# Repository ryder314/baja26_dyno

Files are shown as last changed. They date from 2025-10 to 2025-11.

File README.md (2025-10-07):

# baja26_dyno
All files related to the motor dyno built by/for Texas A&M's Baja SAE 2026

The motor dyno makes use of a mechanical hydraulic pump connected to the
engine, which pumps hydraulic fluid around a tank with a restrictor controlled
by a stepper motor.
The designed PCB makes use of an XFW-HX711 module to read a load cell, an A4988
stepper driver for controlling flow restriction, as well as up to two RPM sensors
for engine RPM and eventually for primary/secondary sheave RPM when testing with
the e-CVT.
The design uses a Luckfox Lyra as the devboard to process and store data. This
board runs Buildroot Linux and handles all reading of inputs, calculation of
outputs, and storage/display of results.

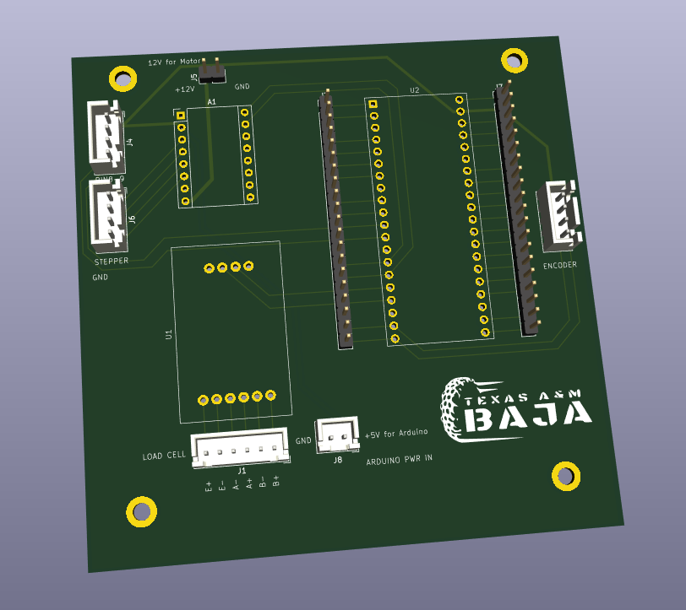
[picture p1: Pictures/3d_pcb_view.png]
3D View of the PCB for the Motor Dyno


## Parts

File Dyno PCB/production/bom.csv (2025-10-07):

Designator | Footprint | Quantity | Value | LCSC Part #
A1 | Pololu_Breakout-16_15.2x20.3mm | 1 | Pololu_Breakout_A4988
J1 | JST_XH_B6B-XH-A_1x06_P2.50mm_Vertical | 1 | Conn_01x06
J2, J4, J6 | JST_XH_B4B-XH-A_1x04_P2.50mm_Vertical | 3 | Conn_01x04
J3, J7 | PinHeader_1x20_P2.54mm_Vertical | 2 | Conn_01x20_Pin
J5 | PinHeader_1x02_P2.54mm_Vertical | 1 | Conn_01x02
J8 | JST_XH_B2B-XH-A_1x02_P2.50mm_Vertical | 1 | Conn_01x02_Socket
U1 | XFW_HX711 | 1 | ~
U2 | Untitled | 1 | ~

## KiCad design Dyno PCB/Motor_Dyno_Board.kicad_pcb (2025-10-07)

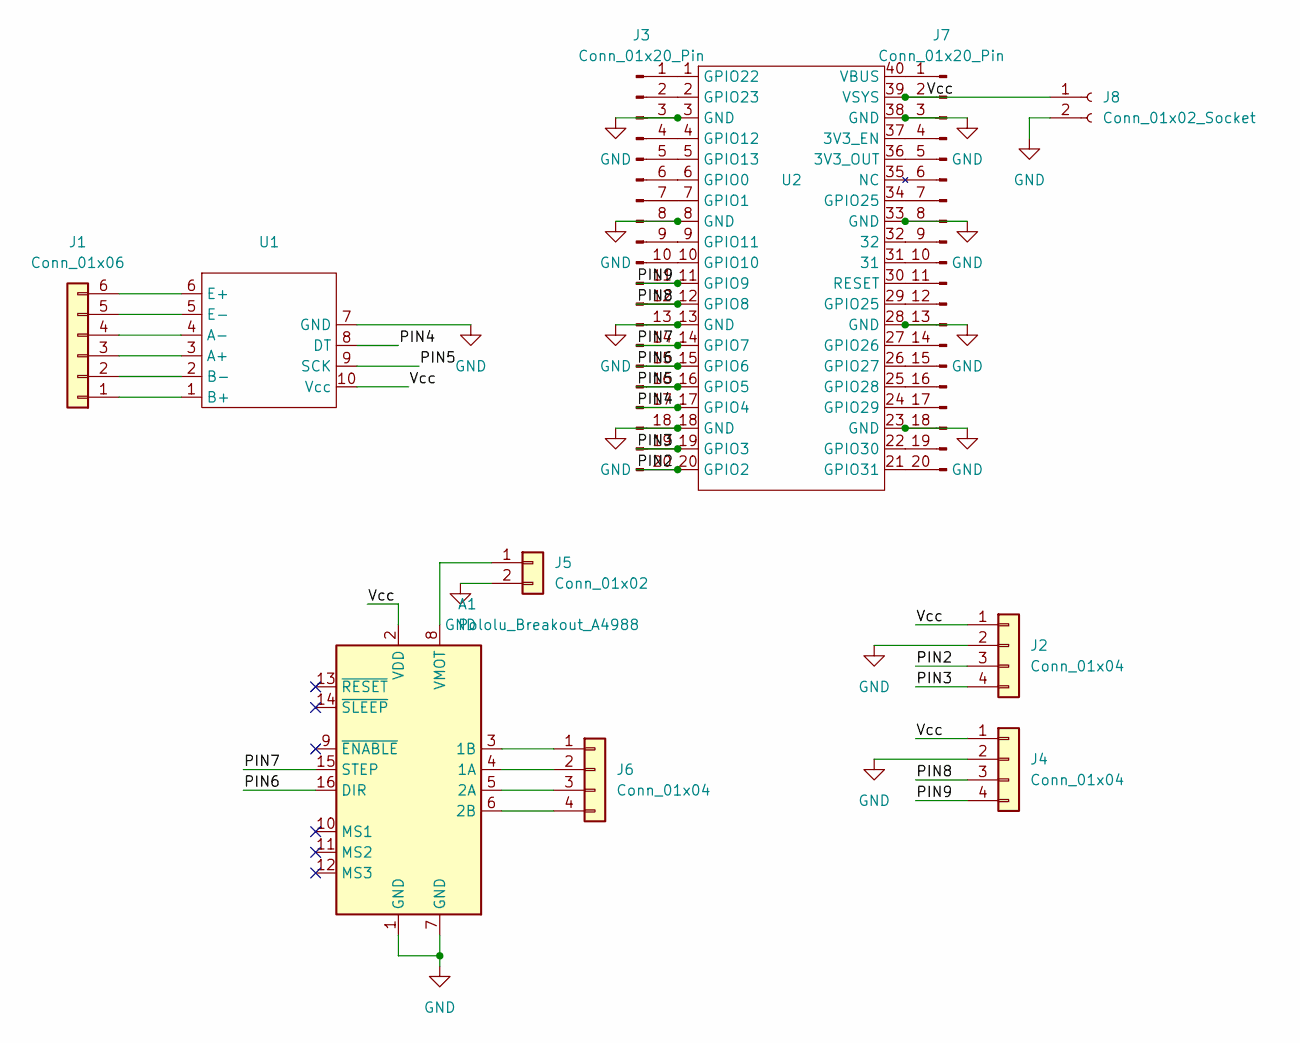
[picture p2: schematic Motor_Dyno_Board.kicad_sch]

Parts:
A1: Pololu_Breakout_A4988; Pololu_Breakout-16_15.2x20.3mm
J1: Conn_01x06; JST_XH_B6B-XH-A_1x06_P2.50mm_Vertical
J2, J4, J6: Conn_01x04; JST_XH_B4B-XH-A_1x04_P2.50mm_Vertical
J3, J7: Conn_01x20_Pin; PinHeader_1x20_P2.54mm_Vertical
J5: Conn_01x02; PinHeader_1x02_P2.54mm_Vertical
J8: Conn_01x02_Socket; JST_XH_B2B-XH-A_1x02_P2.50mm_Vertical
U1: XFW_HX711
U2: Untitled

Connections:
/PIN2: J2.3, J3.20, U2.20 (GPIO2)
/PIN3: J2.4, J3.19, U2.19 (GPIO3)
/PIN4: J3.17, U1.8 (DT), U2.17 (GPIO4)
/PIN5: J3.16, U1.9 (SCK), U2.16 (GPIO5)
/PIN6: A1.16 (DIR), J3.15, U2.15 (GPIO6)
/PIN7: A1.15 (STEP), J3.14, U2.14 (GPIO7)
/PIN8: J3.12, J4.3, U2.12 (GPIO8)
/PIN9: J3.11, J4.4, U2.11 (GPIO9)
/Vcc: A1.2 (VDD), J2.1, J4.1, J7.2, J8.1, U1.10 (Vcc), U2.39 (VSYS)
GND: A1.1 (GND), A1.7 (GND), J2.2, J3.3, J3.8, J3.13, J3.18, J4.2, J5.2, J7.3, J7.8, J7.13, J7.18, J8.2, U1.7 (GND), U2.3 (GND), U2.8 (GND), U2.13 (GND), U2.18 (GND), U2.23 (GND), U2.28 (GND), U2.33 (GND), U2.38 (GND)
unnamed: A1.4 (1A), J6.2
unnamed: A1.3 (1B), J6.1
unnamed: A1.5 (2A), J6.3
unnamed: A1.6 (2B), J6.4
unnamed: A1.8 (VMOT), J5.1
unnamed: J1.1, U1.1 (B+)
unnamed: J1.2, U1.2 (B-)
unnamed: J1.3, U1.3 (A+)
unnamed: J1.4, U1.4 (A-)
unnamed: J1.5, U1.5 (E-)
unnamed: J1.6, U1.6 (E+)
unnamed: J3.1, U2.1 (GPIO22)
unnamed: J3.2, U2.2 (GPIO23)
unnamed: J3.4, U2.4 (GPIO12)
unnamed: J3.5, U2.5 (GPIO13)
unnamed: J3.6, U2.6 (GPIO0)
unnamed: J3.7, U2.7 (GPIO1)
unnamed: J3.9, U2.9 (GPIO11)
unnamed: J3.10, U2.10 (GPIO10)
unnamed: J7.1, U2.40 (VBUS)
unnamed: J7.4, U2.37 (3V3_EN)
unnamed: J7.5, U2.36 (3V3_OUT)
unnamed: J7.7, U2.34 (GPIO25)
unnamed: J7.9, U2.32
unnamed: J7.10, U2.31
unnamed: J7.11, U2.30 (RESET)
unnamed: J7.12, U2.29 (GPIO25)
unnamed: J7.14, U2.27 (GPIO26)
unnamed: J7.15, U2.26 (GPIO27)
unnamed: J7.16, U2.25 (GPIO28)
unnamed: J7.17, U2.24 (GPIO29)
unnamed: J7.19, U2.22 (GPIO30)
unnamed: J7.20, U2.21 (GPIO31)

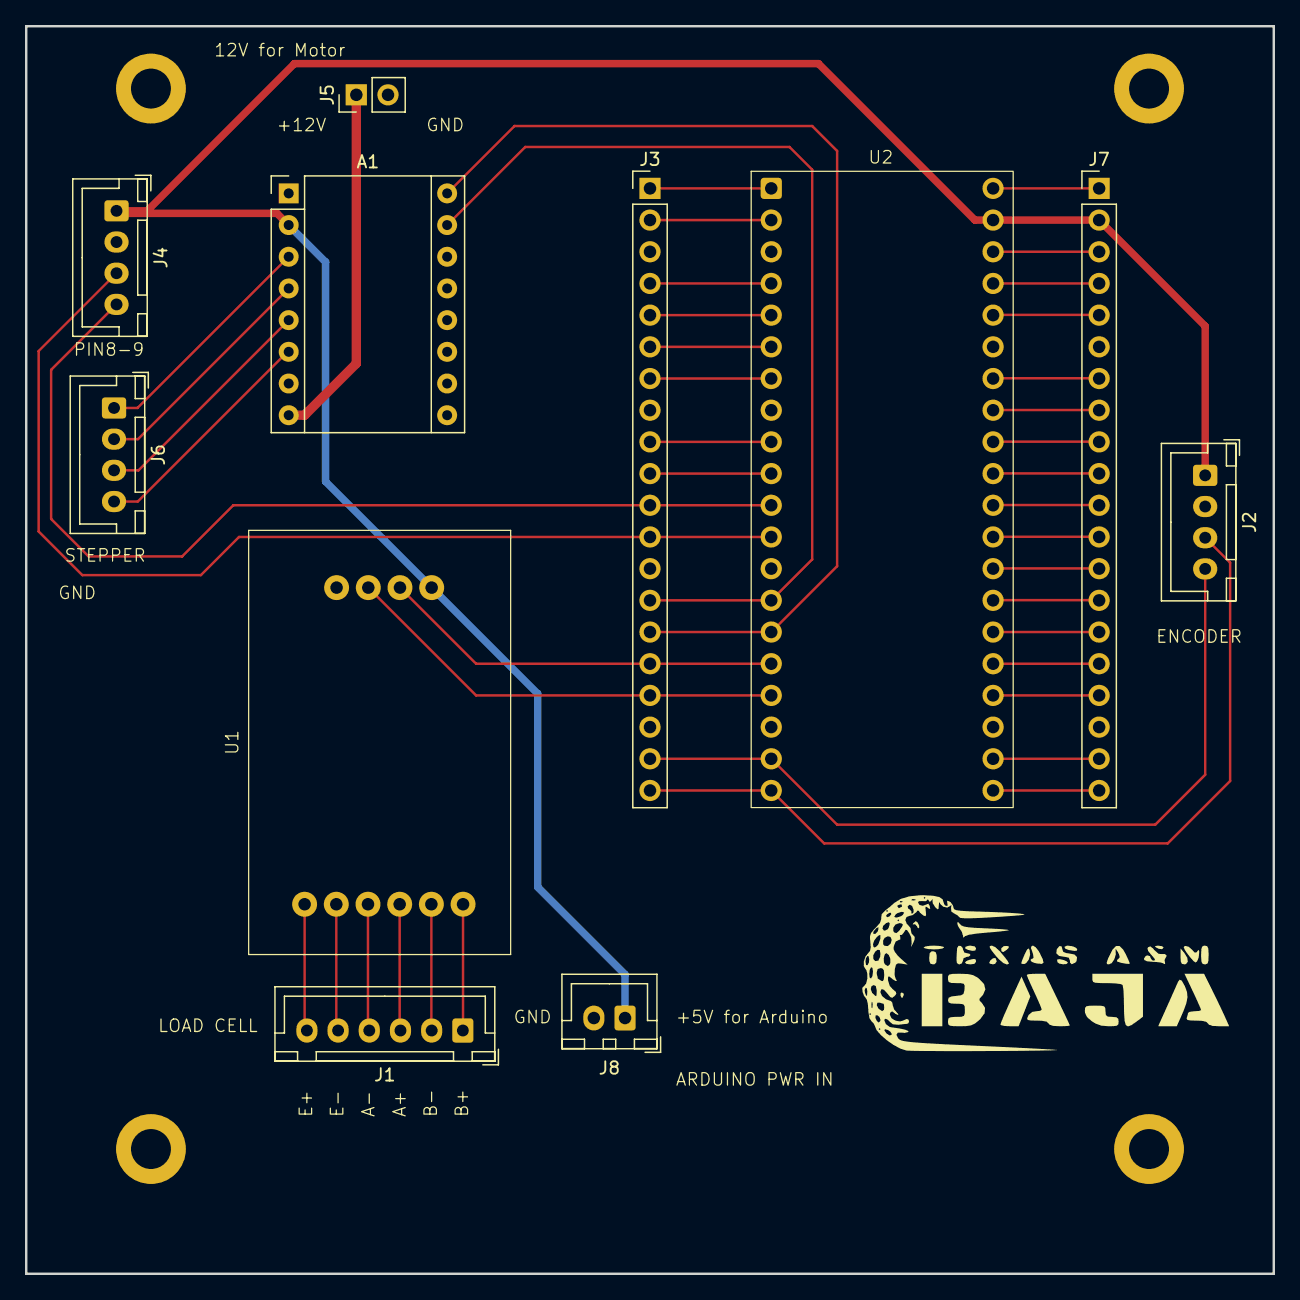
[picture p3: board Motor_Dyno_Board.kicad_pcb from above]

Board: 2 copper layers, 100.0 x 100.0 mm, 11 parts (0 on the bottom side), 43 nets.

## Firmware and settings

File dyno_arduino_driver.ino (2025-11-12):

// ================================
// Dyno Code
// ================================
// Reads two Hall-effect sensors (primary & secondary) on pins 2 and 3
// Reads a load cell w/ a data and clock on pins 5 and 6
// Calculates rotational velocity (RPM) for each sensor
// Scales load cell values to lbs
// Uses interrupts for accurate timing and easy scalability
// ================================
#include "HX711.h"

const int HALL_PRIMARY_PIN   = 3;   // CVT Primary Hall sensor
const int HALL_SECONDARY_PIN = 2;   // CVT Secondary Hall sensor
const int LED_PIN            = 13;  // Built-in LED (optional indicator)
const int LOAD_CELL_DATA     = 5;   // Load Cell Data Pin
const int LOAD_CELL_CLK      = 6;   // Load Cell CLock Pin

HX711 loadCell;
const float LOAD_CELL_SCALE = -42109.1;

// Variables for timing and pulse tracking
volatile unsigned long lastPrimaryTime = 0;
volatile unsigned long lastSecondaryTime = 0;
volatile unsigned long primaryPeriod = 0;
volatile unsigned long secondaryPeriod = 0;

// RPM calculation variables
float primaryRPM = 0.0;
float secondaryRPM = 0.0;
float loadCellValueLbs = 0.0;

// Number of magnets (pulses per revolution)
const int MAGNETS_PER_REV = 1;

// Timing control for serial output
unsigned long lastPrintTime = 0;
unsigned long PRINT_INTERVAL_MS = 0;  // print/log rate in MS -- defined and sent by python file

// ================================
// Interrupt Service Routines
// ================================
void primaryISR() {
  unsigned long now = micros();
  primaryPeriod = now - lastPrimaryTime;
  lastPrimaryTime = now;
}

void secondaryISR() {
  unsigned long now = micros();
  secondaryPeriod = now - lastSecondaryTime;
  lastSecondaryTime = now;
}

// ================================
// Setup
// ================================
void setup() {
  Serial.begin(115200);
  pinMode(HALL_PRIMARY_PIN, INPUT_PULLUP);
  pinMode(HALL_SECONDARY_PIN, INPUT_PULLUP);
  pinMode(LED_PIN, OUTPUT);

  // Attach interrupts for both sensors
  attachInterrupt(digitalPinToInterrupt(HALL_PRIMARY_PIN), primaryISR, FALLING);
  attachInterrupt(digitalPinToInterrupt(HALL_SECONDARY_PIN), secondaryISR, FALLING);

  Serial.println("time,prim_rpm,sec_rpm,load_lbs");

  loadCell.begin(LOAD_CELL_DATA, LOAD_CELL_CLK);
  loadCell.set_scale(LOAD_CELL_SCALE);
  loadCell.tare();
}

// ================================
// Main Loop
// ================================
void loop() {

  if (!digitalRead(HALL_PRIMARY_PIN)) {
    digitalWrite(LED_PIN, HIGH);
  } else {
    digitalWrite(LED_PIN, LOW);
  }

  unsigned long currentMillis = millis();

  // Update and print at fixed intervals
  if (PRINT_INTERVAL_MS != 0 && currentMillis - lastPrintTime >= PRINT_INTERVAL_MS) {
    lastPrintTime = currentMillis;

    // Compute RPM from pulse periods
    noInterrupts();
    unsigned long pPeriod = primaryPeriod;
    unsigned long sPeriod = secondaryPeriod;
    interrupts();

    if (pPeriod > 0)
      primaryRPM = (60.0 * 1e6) / (pPeriod * MAGNETS_PER_REV);
    else
      primaryRPM = 0;

    if (sPeriod > 0)
      secondaryRPM = (60.0 * 1e6) / (sPeriod * MAGNETS_PER_REV);
    else
      secondaryRPM = 0;

    if (loadCell.is_ready()) {
        loadCellValueLbs = loadCell.get_units(1);
    }

    // Print results
    Serial.print(currentMillis / 1000.0, 3);
    Serial.print(",");
    Serial.print(primaryRPM, 0);
    Serial.print(",");
    Serial.print(secondaryRPM, 0);
    Serial.print(",");
    Serial.println(loadCellValueLbs, 2);
    Serial.flush();
  } else if (PRINT_INTERVAL_MS == 0 && Serial.available()) {
    PRINT_INTERVAL_MS = Serial.parseInt();
    Serial.print("# Acknowledged polling rate of ");
    Serial.print(PRINT_INTERVAL_MS);
    Serial.println(" ms.");
    Serial.flush();
  }
}

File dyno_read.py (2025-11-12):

import os
import time
from datetime import datetime
import serial
from serial.tools import list_ports

# --- Config ---
POLLING_RATE_MS = 25
PRINT_RATE_MS = 1000
baud_rate = 115200
preferred_port = "COM9"  # will try this first if it exists

# --- Pick a port robustly ---
ARDUINO_VIDPIDS = {
    (0x2341, 0x0043),  # Arduino Uno (old)
    (0x2341, 0x0001),  # Arduino Uno (rev)
    (0x2A03, 0x0043),  # Arduino (other vendor ID)
    (0x1A86, 0x7523),  # CH340
    (0x10C4, 0xEA60),  # Silicon Labs CP210x
    (0x0403, 0x6001),  # FTDI FT232
}

def choose_serial_port(preferred=None):
    ports = list(list_ports.comports())
    if not ports:
        raise RuntimeError("No serial ports detected. Plug the board in and try again.")
    # If preferred exists, use it
    if preferred:
        for p in ports:
            if p.device.upper() == preferred.upper():
                return p.device
    # Otherwise try to match by VID/PID
    for p in ports:
        if p.vid is not None and p.pid is not None and (p.vid, p.pid) in ARDUINO_VIDPIDS:
            return p.device
    # Fallback to the first port
    return ports[0].device

port = choose_serial_port(preferred_port)
print(f"Using serial port: {port}")

# --- Files ---
out_dir = "saved_data"
os.makedirs(out_dir, exist_ok=True)
FILENAME = os.path.join(out_dir, datetime.now().strftime("dyno_data_%d-%m-%Y, %H-%M.csv"))
print("Saving to:", os.path.abspath(FILENAME))   # <<--- add this


successfully_initialized = False
lastTime = lastPrimVel = lastSecVel = lastLoad = 0.0
lastPrint_ms = time.perf_counter() * 1000

def readyToPrint() -> bool:
    global lastPrint_ms
    now = time.perf_counter() * 1000
    if now - lastPrint_ms >= PRINT_RATE_MS:
        lastPrint_ms = now
        return True
    return False

# --- Open serial (with helpful errors) ---
try:
    ser = serial.Serial(port, baud_rate, timeout=POLLING_RATE_MS / 1000.0)
except serial.SerialException as e:
    # Show what ports *are* available to make debugging obvious
    available = ", ".join(p.device for p in list(list_ports.comports())) or "none"
    raise SystemExit(f"Failed to open {port}: {e}\nAvailable ports: {available}\n"
                     "Close other serial apps and confirm the correct port in Device Manager.")

time.sleep(2.0)
ser.reset_input_buffer()
ser.reset_output_buffer()
ser.write(f"{POLLING_RATE_MS}\n".encode("ascii", errors="ignore"))

data_file = open(FILENAME, "w", buffering=1)

try:
    while True:
        if ser.in_waiting > 0:
            raw = ser.readline()
            try:
                data = raw.decode("utf-8").strip()
            except UnicodeDecodeError:
                data = raw.decode("latin-1", errors="ignore").strip()

            if not data:
                continue

            if ("time" in data) or ("#" in data):
                successfully_initialized = True
                data_file.write(data + "\n")
                if readyToPrint():
                    print(data)
                continue

            if successfully_initialized:
                parts = data.split(",")
                if len(parts) < 4:
                    continue
                try:
                    t, prim, sec, load = map(float, parts[:4])
                except ValueError:
                    continue

                # FIXED comparison parentheses
                if (abs(prim - lastPrimVel) < 100) and (abs(sec - lastSecVel) < 100):
                    data_file.write(data + "\n")
                    if readyToPrint():
                        print(data)

                lastTime, lastPrimVel, lastSecVel, lastLoad = t, prim, sec, load

except KeyboardInterrupt:
    print(f"\nExiting. Test duration (last 'time' field): {lastTime:.2f}")
finally:
    try: data_file.close()
    except: pass
    try: ser.close()
    except: pass

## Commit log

2025-10-07 Updated readme and added PCB design files from v1, ordered 10/7/25
    [Motor_Dyno_Board.kicad_pcb, Motor_Dyno_Board.kicad_sch, bom.csv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]
2025-10-07 Adding picture of PCB for readme
